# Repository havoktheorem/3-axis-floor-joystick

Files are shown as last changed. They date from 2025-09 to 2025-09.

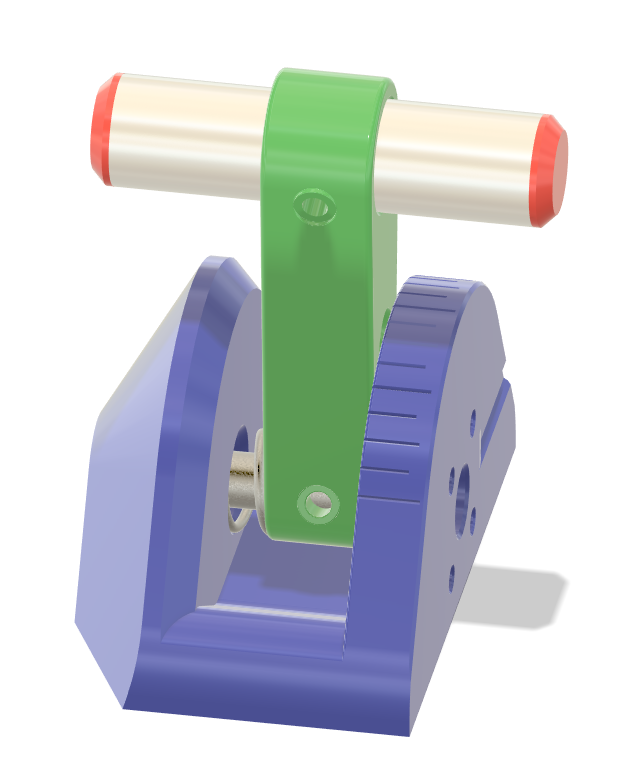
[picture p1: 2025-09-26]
Fusion360_MoPOmk4sG3.png

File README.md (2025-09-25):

# 3-axis-floor-joystick
This is a design based on the Akaki pipechair-cockpit in form factor, but with a total design of the moving assemblies to address issues with stiffness, tolerances and ease of assembly. Apart from 3D printed components, the system uses 16mm aluminium tube for its structure and axles, press-fit plain bearings, and AS5600 rotary encoders for all axes.
All attachment is either by press fit or using M3 and M4 heat-set inserts and screws. I have designed as much as possible to minimise support and make assembly straightforward.

**Rudder assembly:**
I used a clean-sheet design which dispensed with Akaki's transverse axle pedals. I found the angle of the pedals uncomfortably steep and too closely spaced; the pulley system introduced a lot of slop, as did the loose clearance and lack of bearing material around the axle. 
I saw this design as trying to imitate a more expensive sliding pedal assembly, but ultimately introduced more problems than it solved. The alternative I came up with is essentially a bicycle handlebar and stem; after some experimentation I settled on a neat 45 degree axis of rotation, which tracks decently with the natural arc of motion made by the ball of the foot when seated. As with all rotating components in this design, the axle is borne by plain bearings pressed into in the fixed assembly. The length of the pedal bars can be adjusted to the individual, as can the length of the frame. A pair of compression springs provide centering.

**Joystick assembly:**
The nested-axle design is nothing special and follows Akaki's design in approximate form, albeit with a much stiffer construction to handle greater spring forces and avoid flexing in the frame under brisk usage. The X axle is made from the standard 16mm tube and has an 8mm threaded rod through a cross hole (can be attached with hot glue, or you can tap the hole) for the Y axis, both of course riding on plain bearings. Six extension springs provide centering force. The joystick shaft is again 16mm tube and is secured with the same screws that clamp the halves of the joystick carriage together. 

**Control system:**
The joystick uses inexpensive AS5600 encoder boards to measure the angle of each axis, with a magnet fixed to the end of each axle. These are connected to an Arduino (I used a Pro Micro) using the softwarewire library to control three separate I2C devices. I soldered a daughterboard to the back of the Arduino connecting all six I2C pins to VCC with six 3.3kOhm resistors, since the impedance of the built in resistors is too high for fast polling (I suppose - I knew nothing about programming an Arduino until I started using AI to make this thing work). The Joystick library creates an HID device which is identified as a joystick by your sim. The required soldering is not too complex but poor connections can cause major headaches, so prep well.

**Attachment:**
The mounting bracket I designed is to fit a simple metal folding chair by clamping onto its crossbar. You will probably need to design something to fit whatever chair is available to you, or a way to mount it directly to the floor such as with magnets, screws or weights.

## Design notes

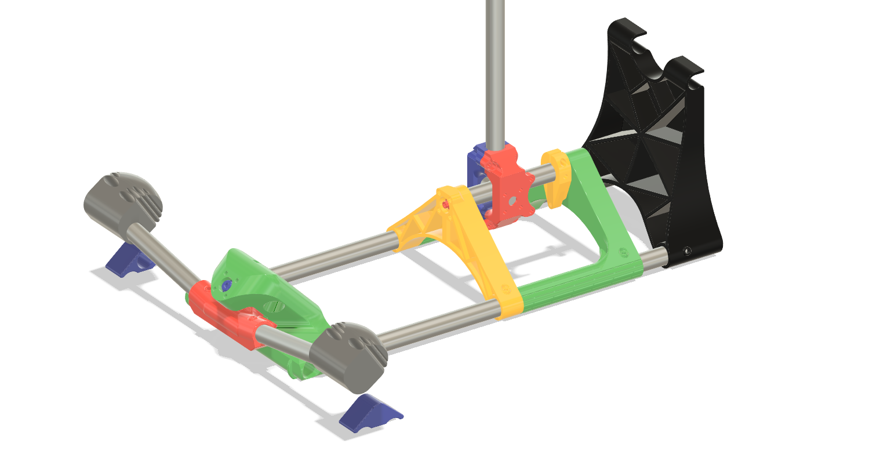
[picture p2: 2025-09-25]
Fusion360_As5dgP8OTv.png

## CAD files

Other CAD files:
throttle joystick v2.f3d
